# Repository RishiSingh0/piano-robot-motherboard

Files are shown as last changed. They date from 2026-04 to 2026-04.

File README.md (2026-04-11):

# Piano Robot Motherboard

STM32F446RET6-based motherboard for a piano-playing robot, designed as part of a university design course. This board serves as the central controller, interfacing with three daughter boards via board-to-board connectors:

- **Actuator control board**: drives the solenoid key-pressing mechanisms
- **Motor control board**: controls motors for lateral positioning along the keyboard
- **Power board**: supplies regulated power to the system

The robot successfully played a complete song in its final demonstration.

<p align="center">
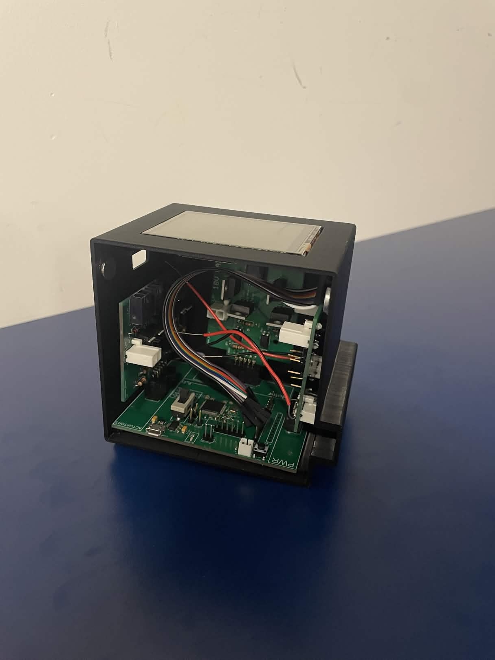
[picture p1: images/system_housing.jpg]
  
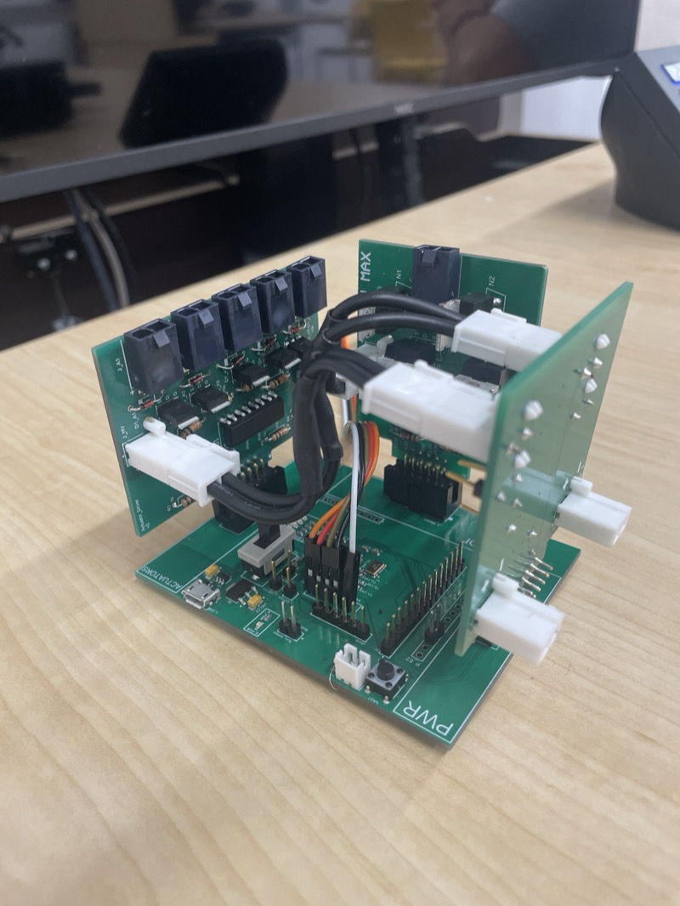
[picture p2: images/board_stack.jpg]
  
</p>
<p align="center">
  <em>Left: Final system in enclosure with ILI9341 LCD. Right: Motherboard with all three daughter boards connected.</em>
</p>

<table>
<tr>
<td align="center" width="50%">
<b>Tuning test</b><br/><br/>
<video src="https://github.com/user-attachments/assets/381959c6-beb1-4cde-a3b7-1b7397a94e4c" width="100%" controls></video>
</td>
<td align="center" width="50%">
<b>Full performance (Fly Me to the Moon)</b><br/><br/>
<video src="https://github.com/user-attachments/assets/a43d4908-bae1-4aea-bd88-e41d0c23e8ff" width="100%" controls></video>
</td>
</tr>
</table>

## Schematic

Full schematic PDF: [`schematic/motherboard_final.pdf`](schematic/motherboard_final.pdf)

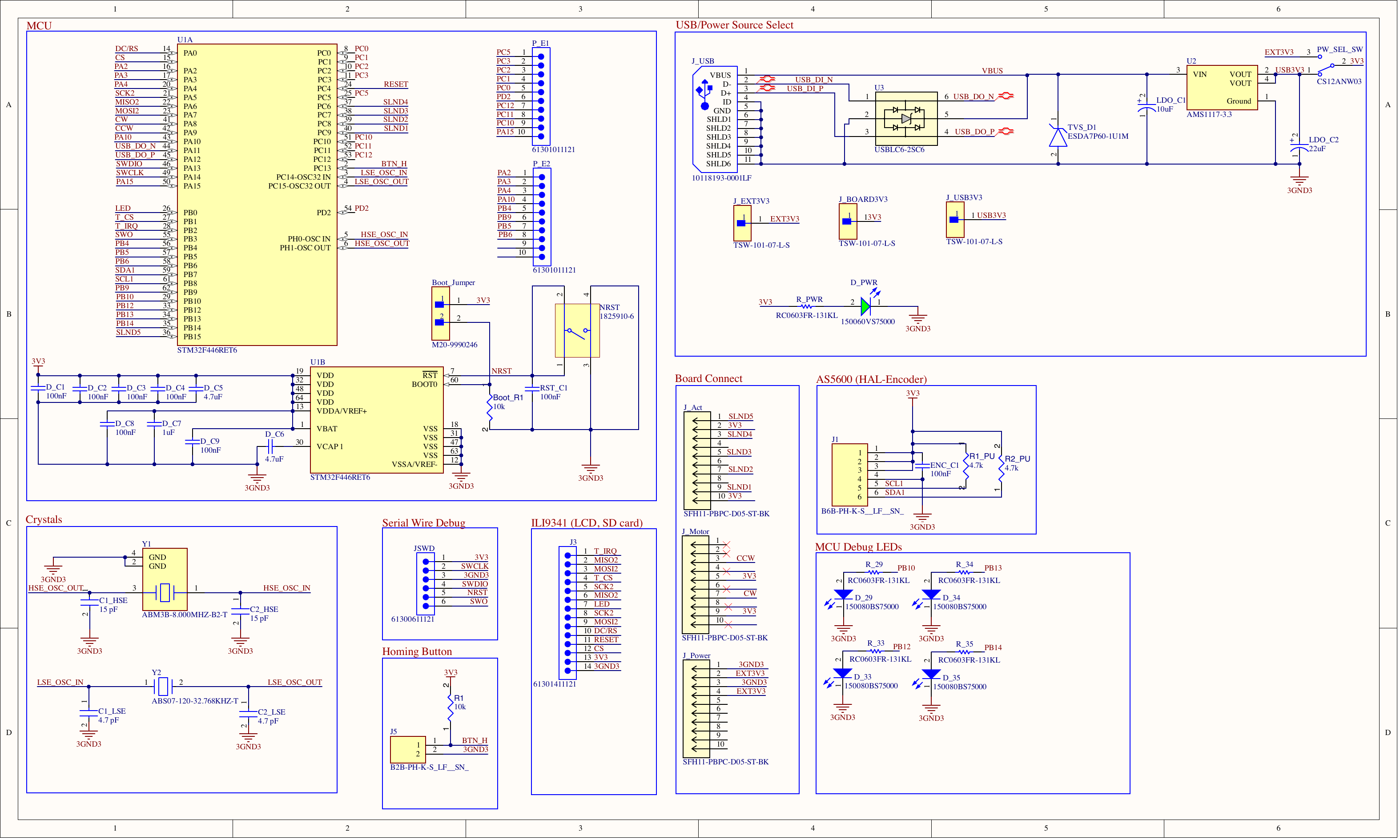
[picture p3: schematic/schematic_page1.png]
Schematic


### MCU: STM32F446RET6 (LQFP64)
- ARM Cortex-M4 with FPU, 180 MHz, 512 KB Flash, 128 KB SRAM
- Chosen for its timer peripherals (motor PWM), ADC channels, and USB OTG FS

### Power Supply
- Dual power source: external 3.3V from power board or USB 5V stepped down via AMS1117-3.3 LDO
- SPDT slide switch (CS12ANW03, break-before-make) selects between the two sources, preventing both from being connected simultaneously
- LDO input: 10uF tantalum, output: 22uF tantalum
- Decoupling follows ST AN4488 recommendations:
  - 4x 100nF (one per VDD pin: 19, 32, 48, 64)
  - 1x 4.7uF bulk cap on VDD
  - 1x 100nF + 1x 1uF on VDDA/VREF+ (pin 13)
  - 1x 4.7uF on VCAP1 (pin 30, internal 1.2V regulator output)
  - 1x 100nF on VBAT (pin 1), tied to VDD with no backup battery
- All VSS/VSSA pins connected to common ground plane
- No PDR_ON or BYPASS_REG pins on LQFP64; internal reset and regulator always enabled (per datasheet Table 4)

### USB (Micro-B, 10118193-0001LF)
- USB OTG FS in device-only mode
- Used for CDC virtual COM port (serial comms) and DFU firmware flashing (via BOOT0 jumper)
- D- (PA11) and D+ (PA12) routed as 90-ohm differential pair
- ESD protection per AN4879 Table 11:
  - USBLC6-2SC6 (SOT-23-6L) on D+/D- data lines, placed close to connector
  - ESDA7P60-1U1M TVS diode on VBUS power line
- USB ID pin tied to GND (device mode)
- USB shield pins tied to GND
- No VBUS sensing; PA9 already used for motor PWM (TIM1_CH2). USB works without it; board is externally powered
- Internal DP pull-up resistor embedded in STM32F446, so no external pull-up needed

### Reset Circuit
- NRST (pin 7) with 100nF filter cap to ground
- Internal 40k pull-up inside the MCU, so no external pull-up resistor needed
- Tact switch (1825910-6, SPST-NO momentary) between NRST and GND for manual reset

### Boot Configuration
- BOOT0 (pin 60) with 10k pull-down to GND, so default boot is from main flash
- 2-pin jumper header (M20-9990246) between BOOT0 and 3V3:
  - Jumper off: boots from flash (normal operation)
  - Jumper on + reset: enters ST built-in bootloader for USB DFU flashing

### Debug: Serial Wire Debug (SWD)
- 6-pin header (2.54mm pitch):
  - Pin 1: 3V3 (VDD_TARGET, voltage reference for ST-LINK, not power supply)
  - Pin 2: SWCLK (PA14)
  - Pin 3: SWDIO (PA13)
  - Pin 4: SWO (PB3), serial debug output via SWV ITM Data Console in CubeIDE
  - Pin 5: NRST
  - Pin 6: GND
- Programmed via Nucleo-F401RE's onboard ST-LINK (CN4 header)
- Remove CN2 jumpers on Nucleo to disconnect its onboard target MCU

### Clocks
- HSE: ABM3B 8 MHz crystal with 2x 15pF load capacitors
- LSE: ABS07-120 32.768 kHz crystal with 2x 4.7pF load capacitors

### Peripherals
- **ILI9341 LCD + SD card**: 14-pin header (SPI + control signals)
- **AS5600 magnetic encoder**: I2C with 4.7k pull-up resistors on SCL/SDA
- **Homing button**: 10k pull-up resistor, active low
- **Debug LEDs**: 4x blue LEDs on PB10, PB12, PB13, PB14 with 1k current-limiting resistors
- **Status LED**: on GPIO
- **Board-to-board connectors**: 3x SFH11-PBPC-D05-ST-BK (10-pin each) for actuator, motor, and power daughter boards
- **SPI header**: 4-pin (SCK2, MISO2, MOSI2, SD_CS)

### GPIO Expansion Headers
Two breakout headers expose spare MCU pins for future peripherals, probing, and debugging:
- **P_E1** (12-pin): PC0, PC1, PC2, PC3, PC4, PC5, PC6, PC7, PD2, PC12, PC10, PA15
- **P_E2** (10-pin): PA2, PA3, PA4, PA10, PB9, PB5, PB6, PB8 + GND

### Motor Interface (via board connector)
- PA8: TIM1_CH1 (PWM signal 1)
- PA9: TIM1_CH2 (PWM signal 2)

## PCB Layout

2-layer board designed in Altium Designer. SMD components hand-soldered using a hot plate.

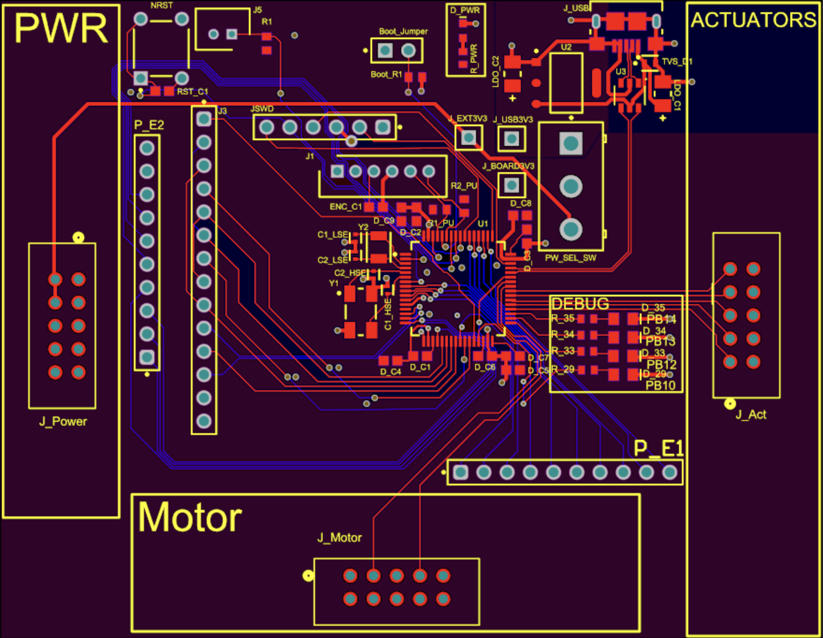
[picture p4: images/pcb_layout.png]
PCB Layout


Key layout decisions:
- Board-to-board connectors (J_Power, J_Motor, J_Act) placed on three edges for vertical daughter board stacking
- USB connector and power switch grouped on the top edge for accessibility
- Decoupling capacitors placed as close to their respective VDD pins as possible
- HSE/LSE crystals placed near MCU oscillator pins with short, symmetric traces
- USB D+/D- routed as a differential pair with ESD protection placed close to the connector
- Debug header and GPIO expansion headers on opposing sides

<p align="center">
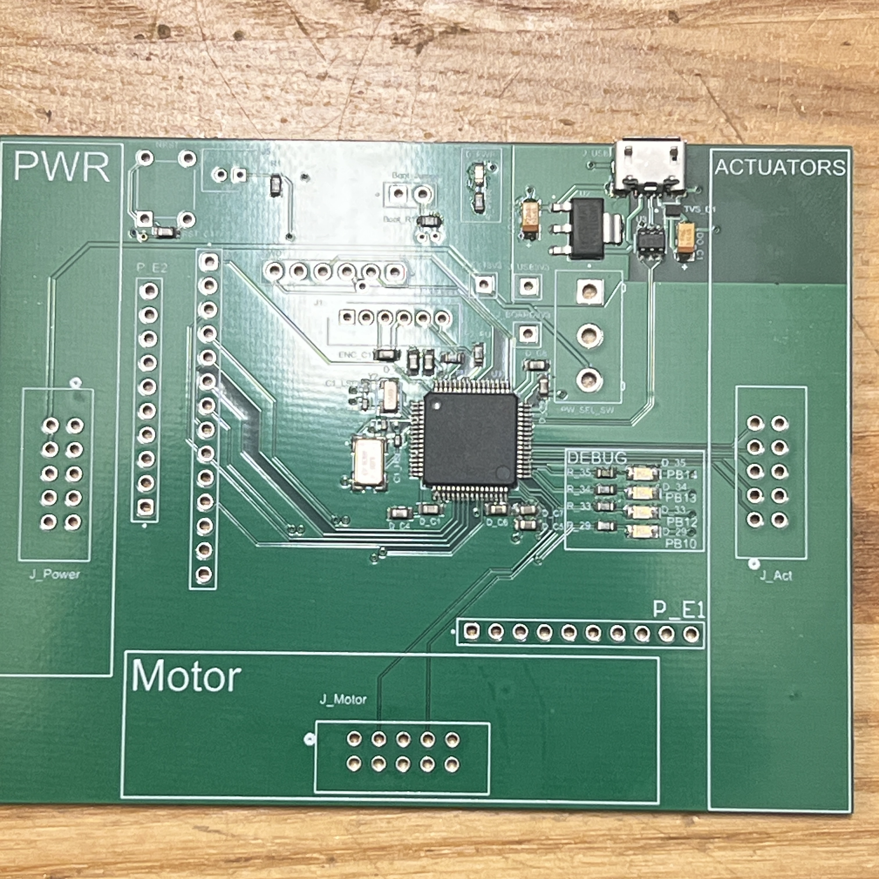
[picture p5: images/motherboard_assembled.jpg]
  
</p>
<p align="center"><em>Motherboard after hot plate reflow soldering.</em></p>

## BOM Summary

| Component | Value | Designator | Qty |
|---|---|---|-----|
| STM32F446RET6 | LQFP64 | U1 | 1 |
| AMS1117-3.3 | 3.3V LDO | U2 | 1 |
| USBLC6-2SC6 | USB ESD | U3 | 1 |
| ESDA7P60-1U1M | VBUS TVS | TVS_D1 | 1 |
| 100nF ceramic | 0603 | D_C1-C4, D_C8, D_C9, RST_C1 | 7 |
| 4.7uF ceramic | 0603 | D_C5, D_C6 | 2 |
| 1uF ceramic | 0603 | D_C7 | 1 |
| 10uF tantalum | 1206 | LDO_C1 | 1 |
| 22uF tantalum | 1206 | LDO_C2 | 1 |
| 15pF ceramic | 0402 | C1_HSE, C2_HSE | 2 |
| 4.7pF ceramic | 0402 | C1_LSE, C2_LSE | 2 |
| 10k resistor | 0603 | Boot_R1, R1 | 2 |
| 4.7k resistor | 0603 | R1_pullup, R2_pullup | 2 |
| 1k resistor (RC0603FR-131KL) | 0603 | R_29, R_33, R_34, R_35 | 4 |
| 150080BS75000 | Blue LED | D_29, D_33, D_34, D_35 | 4 |
| ABM3B 8MHz | Crystal | Y1 | 1 |
| ABS07 32.768kHz | Crystal | Y2 | 1 |
| 10118193-0001LF | USB Micro-B | J_USB | 1 |
| CS12ANW03 | SPDT switch | PW_SEL_SW | 1 |
| 1825910-6 | Tact switch | NRST | 1 |
| M20-9990246 | 2-pin header | Boot_Jumper | 1 |
| SFH11-PBPC-D05-ST-BK | 10-pin connector | J_Act, J_Motor, J_Power | 3 |

## Design Files

Altium Designer source files are in [`hardware/`](hardware/):

| File | Description |
|---|---|
| `Motherboard_stm.PrjPcb` | Altium project file |
| `Motherboard_R2.PcbDoc` | PCB layout (Rev 2) |
| `Interconnect.SchDoc` | Schematic source |
| `Motherboard_stm.BomDoc` | Bill of materials |
| `Motherboard_stm.OutJob` | Output job configuration |

## References
- [STM32F446RE Datasheet (DS10693)](https://www.st.com/resource/en/datasheet/stm32f446re.pdf)
- [AN4488: Getting started with STM32F4 hardware development](https://www.st.com/resource/en/application_note/an4488-getting-started-with-stm32f4xxxx-mcu-hardware-development-stmicroelectronics.pdf)
- [AN4879: USB hardware and PCB guidelines using STM32 MCUs](https://www.st.com/resource/en/application_note/an4879-introduction-to-usb-hardware-and-pcb-guidelines-using-stm32-mcus-stmicroelectronics.pdf)
- [USBLC6-2 Datasheet](https://www.st.com/resource/en/datasheet/usblc6-2.pdf)
- [AMS1117 Datasheet](https://mm.digikey.com/Volume0/opasdata/d220001/medias/docus/5011/AMS1117.pdf)

## Status
Complete. Board was designed, fabricated, assembled (hot plate reflow), and tested. The full system (motherboard + three daughter boards) was integrated into a 3D-printed enclosure and successfully played a song in the final demonstration.

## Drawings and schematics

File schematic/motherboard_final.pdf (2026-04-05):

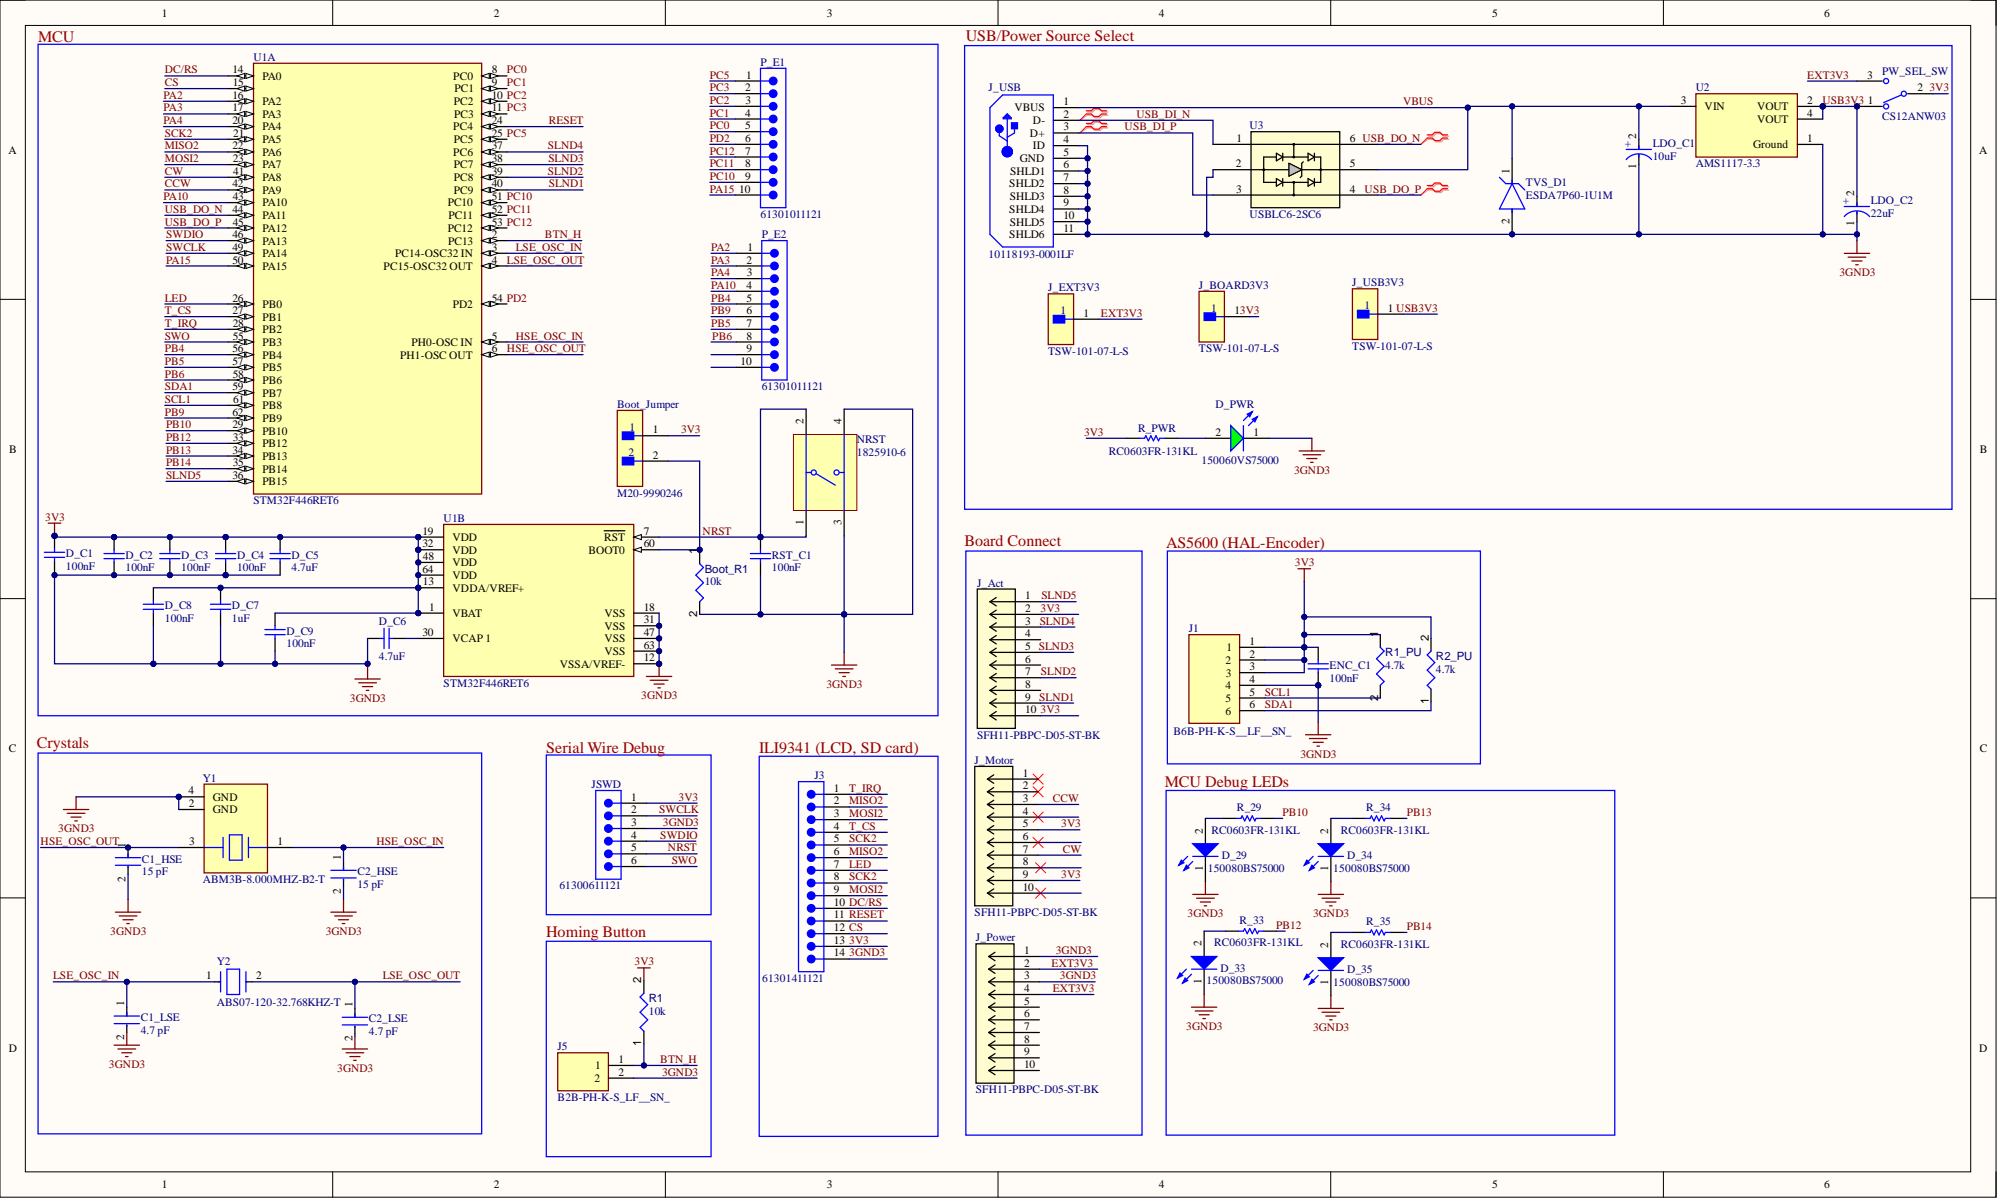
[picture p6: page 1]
0-OSC IN; ILI9341 (LCD; , SD card); Board Connect; ing But; Debug 213456; 1 SHLD5; Debug LED

USB/Power Source Select

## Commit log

2026-03-23 Add reviewed motherboard schematic PDF
2026-03-23 Document complete schematic design decisions and BOM in README
2026-03-23 Add inline schematic images to README
2026-03-23 Remove BOM image, show only schematic
2026-04-05 Update schematic to final revision with GPIO expansion headers
    Replace Interconnect.pdf with motherboard_final.pdf, regenerate the
    README's schematic image from it, and document the new P_E1/P_E2
    GPIO breakout headers exposing spare MCU pins.
2026-04-08 Add PCB layout, assembly photos, Altium source files, and update README
    Repo now reflects the completed project: PCB layout images, hot plate
    assembled board photo, daughter board stack, system in enclosure,
    Altium source files, debug LEDs in BOM, and updated status.
    [Interconnect.SchDoc, Motherboard_stm.PrjPcb]
2026-04-11 Restore demo video in-repo with HTML video embed
    Re-add images/demo.mp4 (recovered from commit ae896a4) and switch the
    README from the GitHub user-attachments URL to an inline <video> tag
    referencing the committed file. The user-attachments asset was garbage
    collected when the repo was briefly deleted, so host the video in-repo
    for durability.
2026-04-11 Embed tuning and full performance videos via user-attachments
    Use the user-attachments URLs for both the tuning test demo and the
    final performance (Fly Me to the Moon), wrapped in centered <p> tags
    at 80% width. Resolves the long-standing TODO for the full performance
    video.
